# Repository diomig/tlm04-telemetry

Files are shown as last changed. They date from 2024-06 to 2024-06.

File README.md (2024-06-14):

# Telemetry System for TLM03e and TLM04e

In automotive racing, every second counts when it comes to winning a race. If the pilot brakes too early or makes too wide of a turn, they risk being overtaken and loosing the advantage. Thus, it is of major interest to be aware of how the vehicle behaves on track. In professional automotive sports, such as Formula 1 and MotoGP, the teams resort to the use of telemetry to improve machine and rider performance. 
This project refers to the telemetry system developed for an electric racing motorcycle prototype, built by Portuguese students at Instituto Superior Técnico (IST). 
[TLMoto](https://tlmoto.tecnico.ulisboa.pt/) is a team made of students, mainly from IST, which is dedicated to projecting, building and racing electric motorcycles for international competitions around the world, like the one shown in the figure bellow.

This telemetry system is equipped with various sensors and communicates with the other sub-systems within the motorcycle, in order to collect and log as much information as possible. This piece of equipment has allowed the team at TLMoto to better understand the behavior of the prototype, advise the rider and also to troubleshoot other parts of the vehicle.

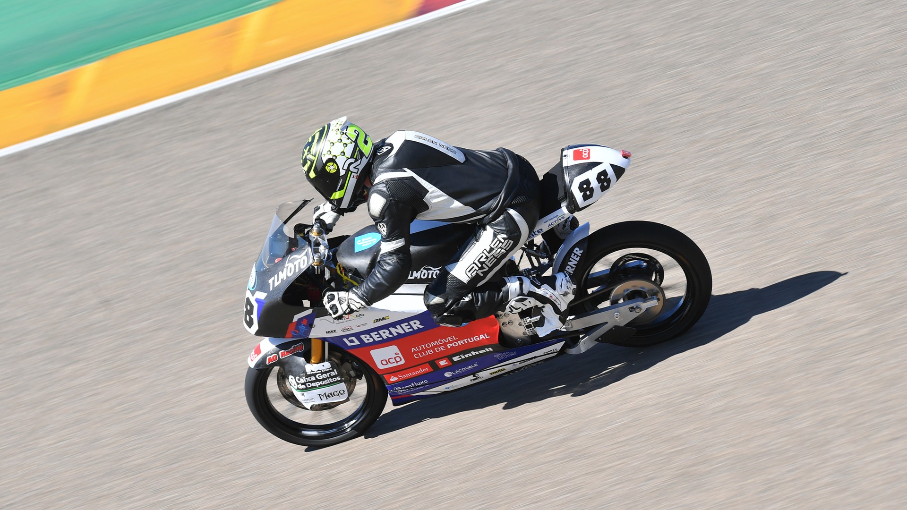
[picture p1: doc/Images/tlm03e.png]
TLM03e prototype TLM03e


## What is telemetry?
Telemetry is the measurement of data from a distant object or vehicle, and, in many cases, the transmission of those measurements to a ground-station or database. However, all the competitions (like MotoStudent:tm:, Moto Engineering Italy:tm:, etc.) prohibit the use of live telemetry data transmission, as is the case of the professional MotoGP. As stated on the official regulation documents of those competitions, the telemetry data obtained from the prototype must only be acquired during pit-stops. 

The telemetry acquisition is a very important sub-system of the prototype, as it allows the team to have an accurate description of its behaviour in tests and races, as well as to provide feedback and suggestions to the pilot. It also plays a big roll in understanding what could be altered on the current prototype or what could be improved on the next one.

## Project Description and Requirements
This system is intended to measure, manage, store and finally transmit all the acquired data, which is then sent to an external computer to be properly processed and displayed to the pit crew. The objective is to extract the maximum of useful data to accurately characterize the prototype, while avoiding to overload the system. For this reason, not only the physical quantities to obtain must be chosen wisely, but also the system must be fast and robust so the loss of information is minimal. It should collect information about the dynamic, mechanical, electrical and thermal aspects of the motorcycle, as well as the control inputs given by the pilot, in order to observe how the prototype actually responds to commands and compare it with the expected response.

The most important items to quantify are: velocity, accelerations, RPM, suspension travel, temperatures of the motor and controller, temperatures of the battery packs, voltages of the battery packs, current from the battery, accelerator and brakes inputs and position over time so the parameters can be analysed along the track. Some other values that are obtained are, for example: phasor components of the motor current ($I_d$, $I_q$), torque, handlebar steering angle, roll and pitch angles, among others. 

As per the data logging and retrieving, all the acquired values are stored during the laps in an SD card, that can be conveniently removed and plugged in to a computer. Alternatively to the removal of the SD card, the content of the telemetry may be transmitted to the computer via Bluetooth, using the Bluetooth 5.0 module included in the system's last iteration. This is done as such because, as mentioned earlier, distant communication is not allowed by the regulation and the retrieving of the data must be done only within the premises of the box.

## Sensors and other components
Before specifying what sensors to get, it is best to figure what is already available in the prototype that can provide information about the parameters mentioned in the previous section.

### Controller
One very important component for our motorcycle and any other electric vehicle is the controller, which is used as an interface between the accumulator and the motor. The TLM03e uses a \emph{Sevcon Gen4 Size 6} controller to turn the 126V of direct current from the battery into three-phase AC voltage for the motor. This device is able to control and measure the motor's rotations per minute (RPM), torque and currents, as well as to keep track of the temperatures of the motor and the controller itself. All those parameters are sent to the CAN bus (Controller Area Network) that connects all the sub-systems of the Low Voltage System and then received by the telemetry module. 

### Battery Management System (BMS)
The accumulator is a set of many battery cells in series and parallel configurations. The one in TLM03e is divided in five battery packs, each made of six sets of cells, and they must be constantly monitored and balanced between each other. This task is accomplished by yet another sub-system called BMS (Battery Management System). The BMS measures the voltage of every individual set of cells and the temperature in three points of every pack. The voltage and temperature values obtained by the BMS are sent to the CAN bus.

### Sensors On-board
The position coordinates of the motorcycle along the track are collected by a GPS module. The chosen module was a GPS 4 Click from MikroE, which has a reasonably good accuracy and can provide an update rate of up to 10 Hz. It outputs messages in the NMEA format with information about the coordinates, UTC time and estimated velocity. We use a "mouse" antenna outside the carbon fiber fairing to avoid RF shielding.

The accelerations and rotation angles -- mainly from pitch and roll -- acting on the motorcycle are measured by an Inertial Measurement Unit, or  IMU, based on the ICM-20948 microchip. It includes a three axis accelerometer, a three axis gyroscope and a three axis magnetometer, thus providing nine degrees of freedom.

The suspension travel is obtained with the use of two linear potentiometers, one for the front suspension and one for rear one. A linear potentiometer translates a variable resistance into a linear displacement. This solution requires constant contact between the wiper and the resistive path, which may reduce durability due to friction. An alternative would be a LVDT, however this uses AC signals, requiring more complex implementation on the circuit.

The accelerator handle includes a rotary potentiometer in order to measure the acceleration inputs from the pilot. Its terminals are directly connected to the controller as this is what will determine the mechanical power requested to the motor. The value corresponding to the accelerator knob is also sent to the telemetry system via CAN.

It is noteworthy to mention that our prototype does not have a gearbox, much like the vast majority of electric vehicles, meaning that the linear velocity can very easily be calculated from the motor RPM. This is due to the direct link between the motor shaft and the wheel sprocket, as shown in the figure below. In fact, the velocity is directly proportional to the RPM according to the following expression: 

$$ v[km/h] = \frac{rpm\times2\pi\times r_{wheel}}{60}\times R_G\times \frac{3600}{1000}     $$

where $r_{wheel}$ is the outer radius of the tire and $R_G$ is the gear ratio used for this conversion.

<p align="center">
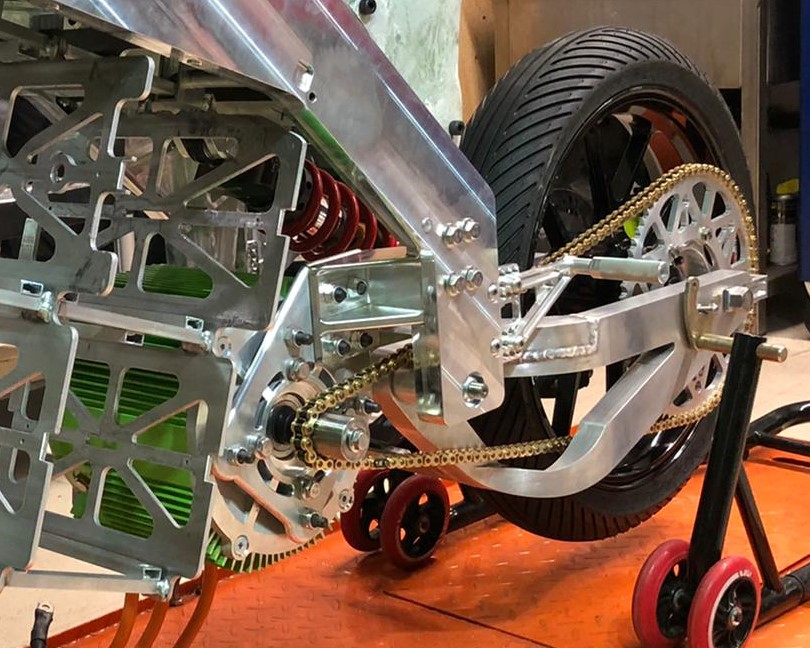
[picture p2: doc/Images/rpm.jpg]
Link between the motor shaft and the wheel sprocket
    
</p>

## PCB
The schematic and layout were made in Altium Designer, the board was manufactured at JLCPCB and it was soldered at TLMoto's workshop in IST. The figure represents only the top layer of the PCB, so some connections are not visible because they are in the bottom layer.

This board includes all sensors and components described above, all commanded by a STM32 microcontroller at the very center. The microcontroller is responsible for collecting, buffering and periodically loading the data to the SD card. It also includes a CAN transceiver and dual Ethernet port for the CAN bus and also for power.

The board operates at 3.3V and requires 5V for some devices. It may be powered through a mini-USB, while programming and debugging, but during its normal operation, it is supplied by the bus that connects the whole Low Voltage System of the motorcycle.

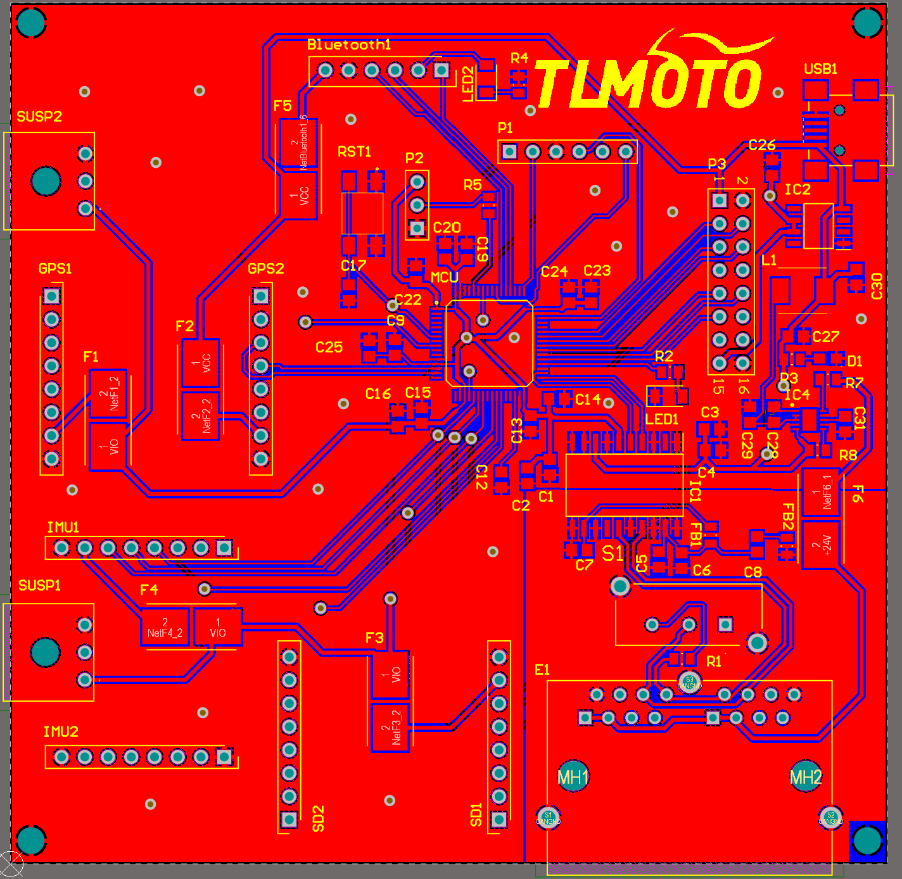
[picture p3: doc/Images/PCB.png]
PCB


## Data Handling and Integration with other subsystems

The GPS module sends the time, coordinates and speed via UART in the format of NMEA strings. 
The CAN messages are arranged according to this table. 

<table>
  <thead>
    <tr>
      <th rowspan="2">CAN ID</th>
      <th colspan="8">Bytes</th>
    </tr>
    <tr>
      <th>B1</th>
      <th>B2</th>
      <th>B3</th>
      <th>B4</th>
      <th>B5</th>
      <th>B6</th>
      <th>B7</th>
      <th>B8</th>
    </tr>
  </thead>
  <tbody>
    <tr>
      <td>11</td>
      <td colspan="2">Target $I_d$</td>
      <td colspan="2">Target $I_q$</td>
      <td colspan="2">$I_f$</td>
      <td colspan="2">$I_q$</td>
    </tr>
    <tr>
      <td>12</td>
      <td colspan="2">$U_d$</td>
      <td colspan="2">$U_q$</td>
      <td colspan="2">Motor PWM</td>
      <td colspan="2">AC Volt.</td>
    </tr>
    <tr>
      <td>13</td>
      <td colspan="2">AC Curr.</td>
      <td colspan="2">Max $I_q$</td>
      <td colspan="2">Motor Temp.</td>
      <td colspan="2">Battery Volt.</td>
    </tr>
    <tr>
      <td>14</td>
      <td colspan="2">Cap. Volt.</td>
      <td colspan="2">Controller Temp.</td>
      <td colspan="2">Battery Curr.</td>
      <td colspan="2">Torque</td>
    </tr>
    <tr>
      <td>15</td>
      <td colspan="4">RPM</td>
      <td colspan="2">Throttle Volt.</td>
      <td colspan="2">Throttle Value</td>
    </tr>
    <tr>
      <td>51</td>
      <td colspan="8">Cell Voltages of Pack 1</td>
    </tr>
    <tr>
      <td>52</td>
      <td colspan="8">Cell Voltages of Pack 2</td>
    </tr>
    <tr>
      <td>53</td>
      <td colspan="8">Cell Voltages of Pack 3</td>
    </tr>
    <tr>
      <td>54</td>
      <td colspan="8">Cell Voltages of Pack 4</td>
    </tr>
    <tr>
      <td>55</td>
      <td colspan="8">Cell Voltages of Pack 5</td>
    </tr>
    <tr>
      <td>121</td>
      <td colspan="8">Temperatures in Packs 1 and 2</td>
    </tr>
    <tr>
      <td>122</td>
      <td colspan="8">Temperatures in Packs 3 and 4</td>
    </tr>
    <tr>
      <td>123</td>
      <td colspan="8">Temperatures in Pack 5</td>
    </tr>
  </tbody>
</table>

All the collected parameters are organized and logged into the SD card, in a CSV file (comma-separated values). This file is then loaded to a computer, which will process the data and generate the desired graphs. 

## Test Results

In this section are shown a few of the many graphs generated from the data acquired while testing the TLM03e in the KIRO (Kartódromo Internacional da Região Oeste) track in Bombarral. Although the telemetry system described in this document was made for TLM04e, this motorcycle is still in development. Thus, the tests were performed with the previous prototype, since this is a modular block compatible with the rest of the system. 

Velocity along the track | Throttle position along the track
--- | ---
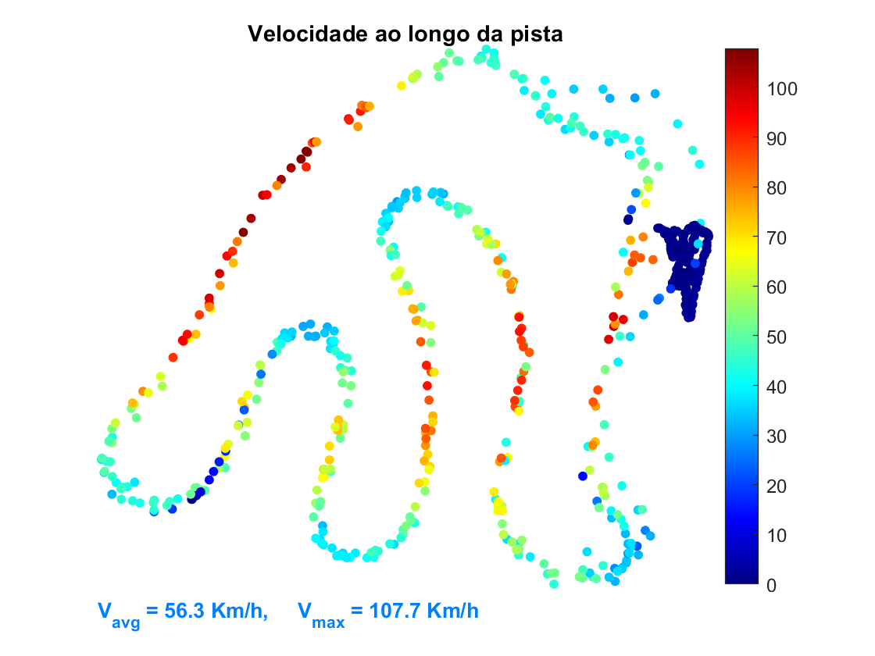
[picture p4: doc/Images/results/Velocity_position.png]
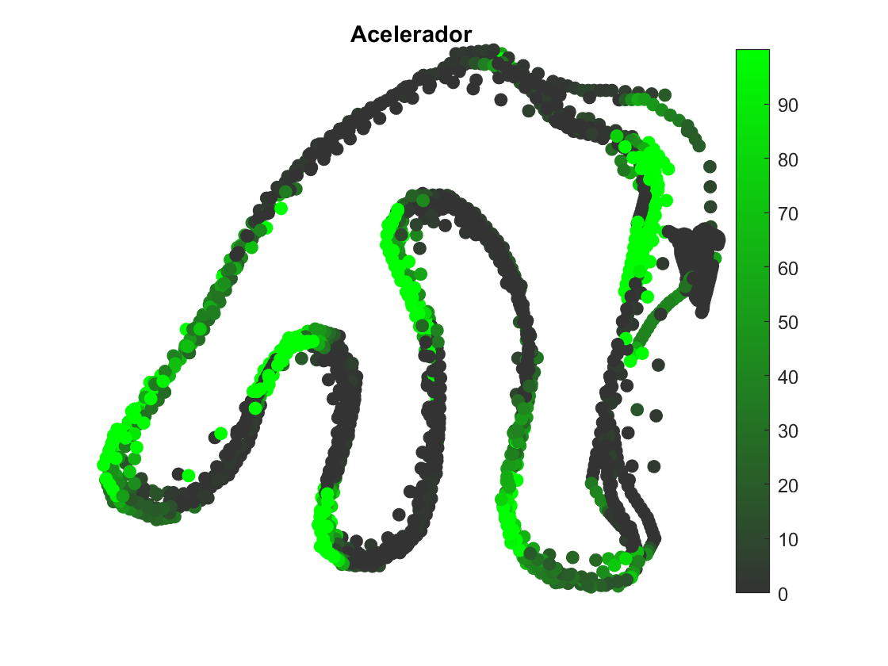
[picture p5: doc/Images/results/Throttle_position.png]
 |  

Speed reaction to the throttle | Motor currents (I_d and I_q)
--- | ---
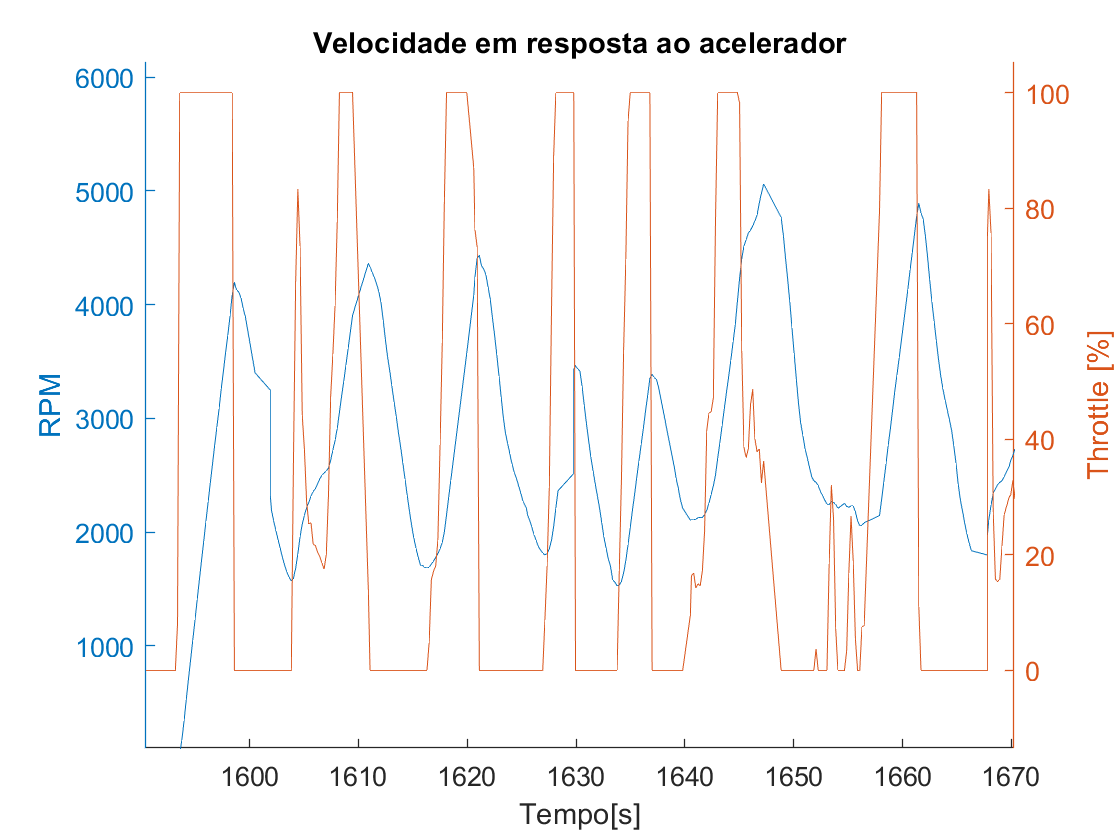
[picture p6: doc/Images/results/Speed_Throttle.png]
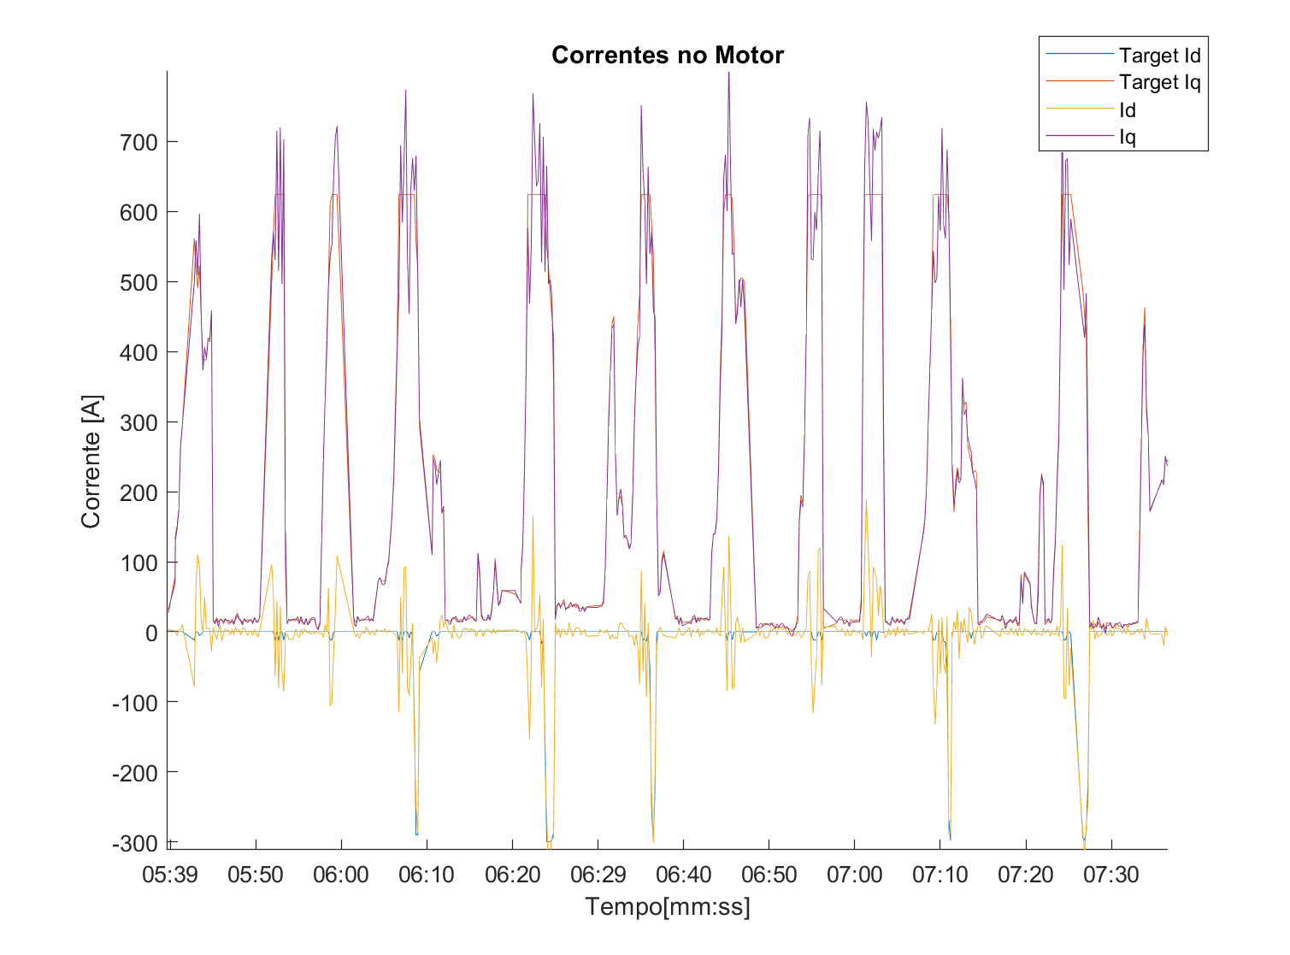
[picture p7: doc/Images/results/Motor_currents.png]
 | 

Battery Voltage | Temperatures of the Motor and Controller
--- | ---
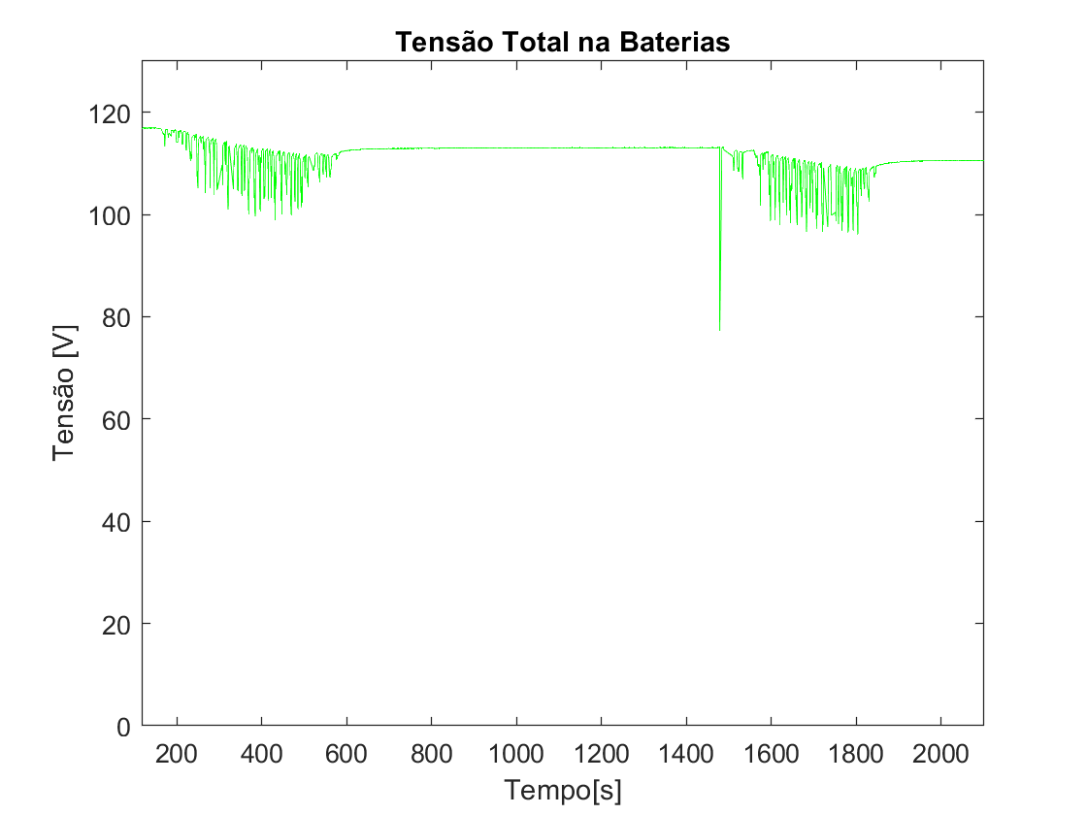
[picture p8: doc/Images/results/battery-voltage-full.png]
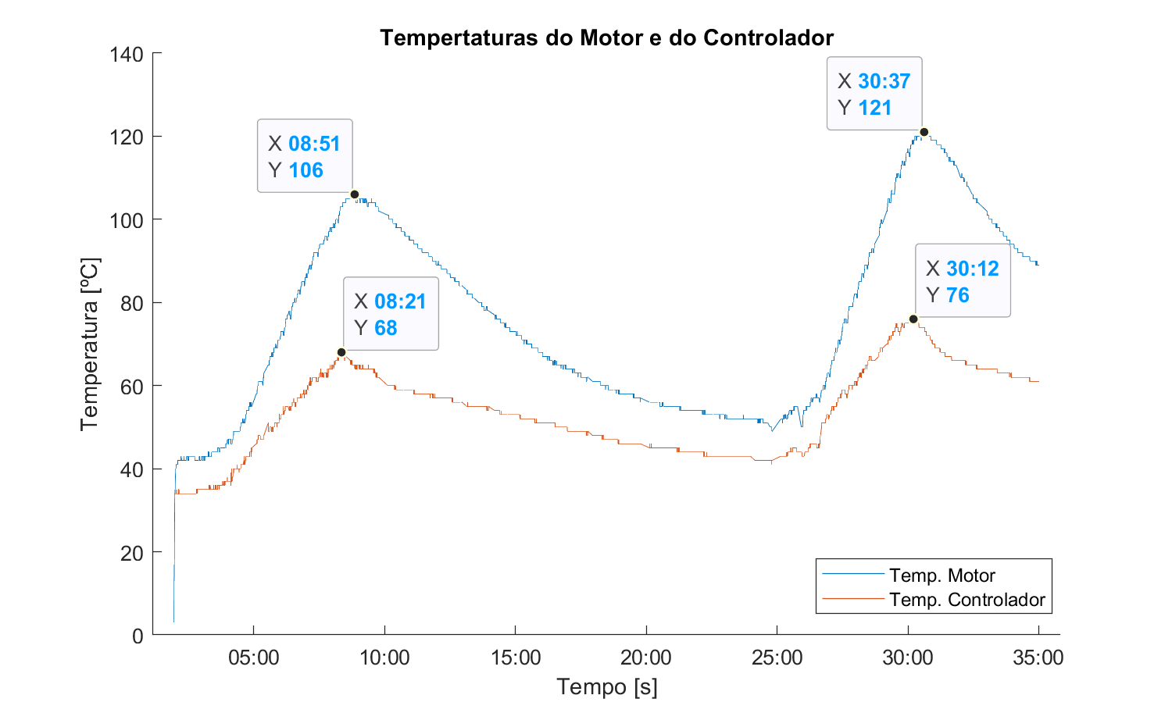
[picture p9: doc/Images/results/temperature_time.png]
 |  

### Motor temperature along the track
<p float="left">
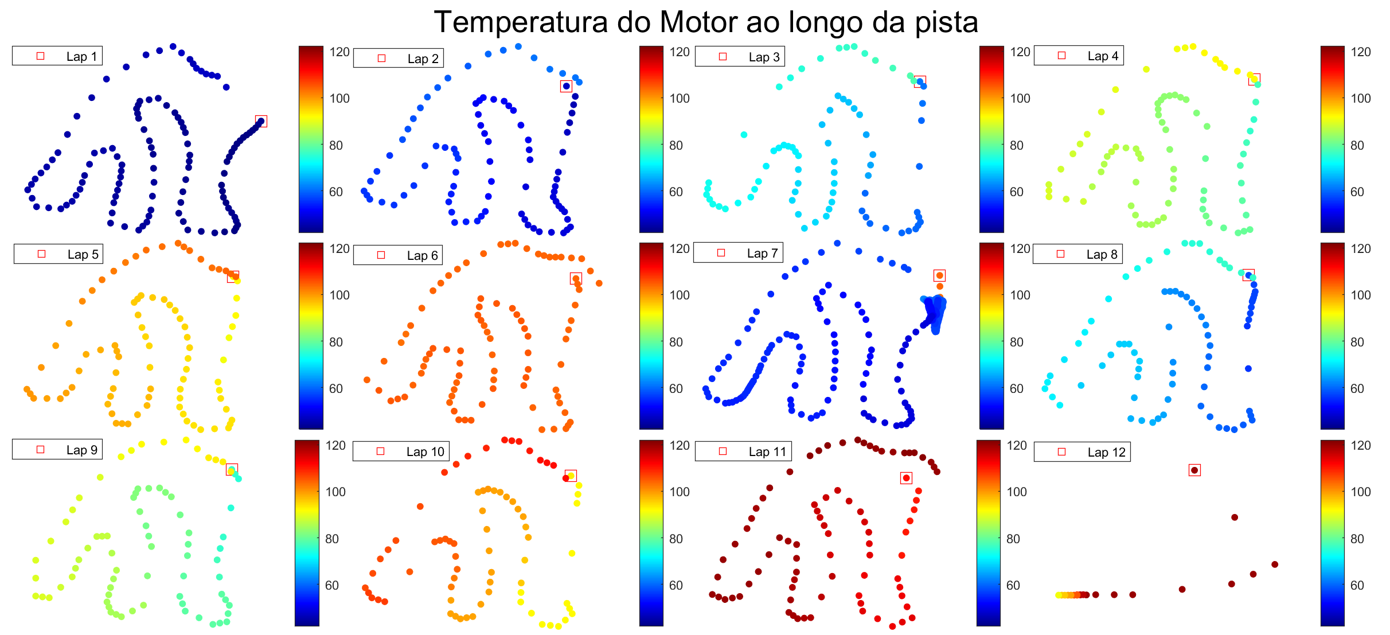
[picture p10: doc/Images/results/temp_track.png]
  
</p>

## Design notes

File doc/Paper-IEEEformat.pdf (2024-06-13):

MEE SOFTSKILLS II, 2022-2023 | 1

# Data Acquisition and Logging System for Electric Motorcycle Prototype

Diogo Lu´ıs
Dept. of Electrical and Computers Engineering IST, University of Lisbon
Lisbon, Portugal
diogo.m.luis@tecnico.ulisboa.pt

Abstract—In automotive racing, every second counts when it comes to winning a race. If the pilot brakes too early or makes too wide of a turn, they risk being overtaken and loosing the advantage. Thus, it is of major interest to be aware of how the vehicle behaves on track. In professional automotive sports, such as Formula 1 and MotoGP, the teams resort to the use of telemetry to improve machine and rider performance. This article refers to the telemetry system developed for an electric racing motorcycle prototype, built by Portuguese students at Instituto Superior Tecnico. This telemetry system is equipped with various ´ sensors and communicates with the other sub-systems within the motorcycle, in order to collect and log as much information as possible. This piece of equipment has allowed the team at TLMoto to better understand the behavior of the prototype, advise the rider and also to troubleshoot other parts of the vehicle.

Index Terms—telemetry, data acquisition, data logging, sensors, racing motorcycle

I. INTRODUCTION
T
LMOTO is a team made of students, mainly from IST, which is dedicated to projecting, building and racing electric motorcycles for international competitions around the world, like the one shown in figure 1. This team is made up of various technical and non-technical departments such as: aerodynamics and cooling, dynamics, electronics, powertrain, structures, marketing, management and sponsors. This project is developed within the scope of the electronics department, more specifically, the telemetry sub-department. Telemetry is the measurement of data from a distant object or vehicle, and, in many cases, the transmission of those measurements to a ground-station or database [1]. However, all the competitions (like MotoStudent™, Moto Engineering Italy™, etc.) prohibit the use of live telemetry data transmission, as is the case of the professional MotoGP. As stated on the official regulation documents of those competitions, the telemetry data obtained from the prototype must only be acquired during pit-stops. This paper describes the development and functioning of the telemetry system built for the next TLMoto prototype, TLM04e. The telemetry acquisition is a very important sub-system of the prototype, as it allows the team to have an accurate description of its behaviour in tests and races, as well as to provide feedback and suggestions to the pilot. It also plays a big roll in understanding what could be altered on the current prototype or what could be improved on the next one [2].


Fig. 1. TLM03e

II. DESIRED FUNCTIONS

This system is intended to measure, manage, store and finally transmit all the acquired data, which is then sent to an external computer to be properly processed and displayed to the pit crew. The objective is to extract the maximum of useful data to accurately characterize the prototype, while avoiding to overload the system. For this reason, not only the physical quantities to obtain must be chosen wisely, but also the system must be fast and robust so the loss of information is minimal. It should collect information about the dynamic, mechanical, electrical and thermal aspects of the motorcycle, as well as the control inputs given by the pilot, in order to observe how the prototype actually responds to commands and compare it with the expected response.
The most important items to quantify are: velocity, accelerations, RPM, suspension travel, temperatures of the motor and controller, temperatures of the battery packs, voltages of the battery packs, current from the battery, accelerator and brakes inputs and position over time so the parameters can be analysed along the track. Some other values that are obtained are, for example: phasor components of the motor current (Id, Iq), torque, handlebar steering angle, roll and pitch angles, among others.
As per the data logging and retrieving, all the acquired values are stored during the laps in an SD card, that can be conveniently removed and plugged in to a computer. Alternatively to the removal of the SD card, the content of the telemetry may be transmitted to the computer via Bluetooth, using the Bluetooth 5.0 module included in the system’s last iteration. This is done as such because, as mentioned earlier, distant communication is not allowed by the regulation and the retrieving of the data must be done only within the premises of the box.

III. SENSORS AND OTHER COMPONENTS
Before specifying what sensors to get, it is best to figure what is already available in the prototype that can provide information about the parameters mentioned in section II.
A. Controller
One very important component for our motorcycle and any other electric vehicle is the controller [3], which is used as an interface between the accumulator and the motor. The TLM03e uses a Sevcon Gen4 Size 6 controller to turn the 126V of direct current from the battery into three-phase AC voltage for the motor. This device is able to control and measure the motor’s rotations per minute (RPM), torque and currents, as well as to keep track of the temperatures of the motor and the controller itself. All those parameters are sent to the CAN bus (Controller Area Network) that connects all the sub-systems of the Low Voltage System and then received by the telemetry module.
B. Battery Management System
The accumulator is a set of many battery cells in series and parallel configurations. The one in TLM03e is divided in five battery packs, each made of six sets of cells, and they must be constantly monitored and balanced between each other. This task is accomplished by yet another sub-system called BMS (Battery Management System)[4]. The BMS measures the voltage of every individual set of cells and the temperature in three points of every pack. The voltage and temperature values obtained by the BMS are sent to the CAN bus.
C. On-board Sensors
The position coordinates of the motorcycle along the track are collected by a GPS module. The chosen module was a GPS 4 Click from MikroE, which has a reasonably good accuracy and can provide an update rate of up to 10 Hz. It outputs messages in the NMEA format with information about the coordinates, UTC time and estimated velocity. We use a ”mouse” antenna outside the carbon fiber fairing to avoid RF shielding.
The accelerations and rotation angles – mainly from pitch and roll – acting on the motorcycle are measured by an Inertial Measurement Unit, or IMU, based on the ICM-20948 microchip. It includes a three axis accelerometer, a three axis gyroscope and a three axis magnetometer, thus providing nine degrees of freedom.
The suspension travel is obtained with the use of two linear potentiometers, one for the front suspension and one for rear one. A linear potentiometer translates a variable resistance into a linear displacement. This solution requires constant contact between the wiper and the resistive path, which may reduce durability due to friction. An alternative would be a

LVDT, however this uses AC signals, requiring more complex implementation on the circuit.
The accelerator handle includes a rotary potentiometer in order to measure the acceleration inputs from the pilot. Its terminals are directly connected to the controller as this is what will determine the mechanical power requested to the motor. The value corresponding to the accelerator knob is also sent to the telemetry system via CAN.

It is noteworthy to mention that our prototype does not have a gearbox, much like the vast majority of electric vehicles, meaning that the linear velocity can very easily be calculated from the motor RPM. This is due to the direct link between the motor shaft and the wheel sprocket, as shown in figure
2. In fact, the velocity is directly proportional to the RPM according to equation 1:

v[km/h] = rpm × 2π × rwheel
60

× RG ×

3600
1000

(1)

where rwheel is the outer radius of the tire and RG is the gear ratio used for this conversion.


Fig. 2. Link between the motor shaft and the wheel sprocket

This method is fairly reliable and allows to get a complementary value of velocity to the GPS with no additional sensors. There is, however, some error associated with the rear wheel drifting on the track, but this appears to be residual as the prototype has considerable downforce [5], specially at high speeds.

IV. HARDWARE AND PCB DESIGN
Figure 3 illustrates the PCB layout from the latest design of the telemetry system. The schematic and layout were made in Altium Designer, the board was manufactured at JLCPCB and it was soldered at TLMoto’s workshop in IST. The figure represents only the top layer of the PCB, so some connections are not visible because they are in the bottom layer.
This board includes all sensors and components described above, all commanded by a STM32 microcontroller at the very center. The microcontroller is responsible for collecting, buffering and periodically loading the data to the SD card. It also includes a CAN transceiver and dual Ethernet port for the CAN bus and also for power.
The board operates at 3.3V and requires 5V for some devices. It may be powered through a mini-USB, while programming and debugging, but during its normal operation, it is supplied by the bus that connects the whole Low Voltage System of the motorcycle.

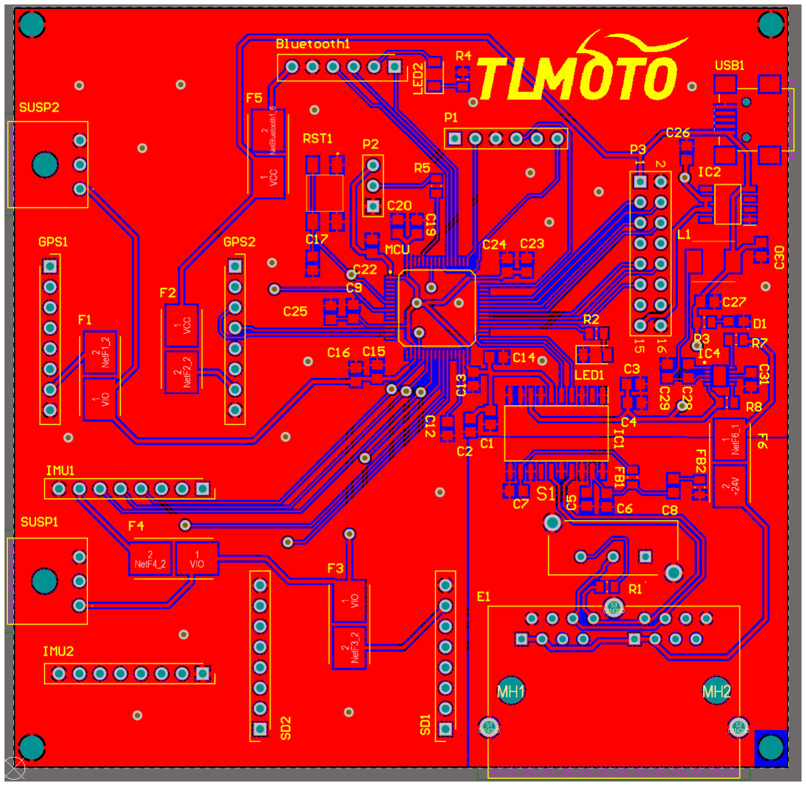
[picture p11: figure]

Fig. 3. Printed Circuit Board of the telemetry system

V. HANDLING THE DATA
The GPS module sends the time, coordinates and speed via UART in the format of NMEA strings. The CAN messages are arranged according to table I.

TABLE I
CAN MESSAGES SENT FROM THE CONTROLLER AND FROM THE BMS
CAN ID | Bytes
B1 | B2 | B3 | B4 | B5 | B6 | B7 | B8
11 | Target Id | Target Iq | If | Iq
12 | Ud | Uq | Motor PWM | AC Volt.
13 | AC Curr. | Max Iq | Motor Temp. | Battery Volt.
14 | Cap. Volt. | Controller Temp. | Battery Curr. | Torque
15 | RPM | | Throttle Volt. | Throttle Value
51 | Cell Voltages of Pack 1
52 | Cell Voltages of Pack 2
53 | Cell Voltages of Pack 3
54 | Cell Voltages of Pack 4
55 | Cell Voltages of Pack 5
121 | Temperatures in Packs 1 and 2
122 | Temperatures in Packs 3 and 4
123 | Temperatures in Pack 5

Controller

BMS

All the collected parameters are organized and logged into the SD card, in a CSV file (comma-separated values). This file is then loaded to a computer, which will process the data and generate the desired graphs.

VI. RESULTS
In this section are shown a few of the many graphs generated from the data acquired while testing the TLM03e in the
KIRO (Kartodromo Internacional da Regi ´ | ao Oeste) track in ˜
Bombarral. Although the telemetry system described in this document was made for TLM04e, this motorcycle is still in development. Thus, the tests were performed with the previous prototype, since this is a modular block compatible with the rest of the system.
In figure 4, it is shown the route of the motorcycle, in the shape of the KIRO track. The color of each point represents its instantaneous velocity according to the color bar to the right. From the image it is clear that, predictably, the speed is lower on the turns and substantially increases in straight lines.

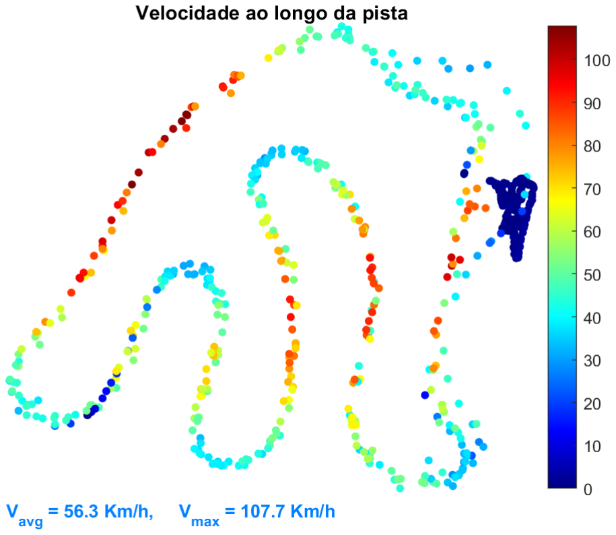
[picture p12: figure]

Fig. 4. Velocity along the track

Figure 5 shows the value of the throttle handle potentiometer along the track. The brightest shade of green means the throttle value is 100% and the darkest shade means that the handle is released. As can be observed, the rider accelerates more at the end of every turn. This information can be interpreted by the pit crew in order to advise the rider.

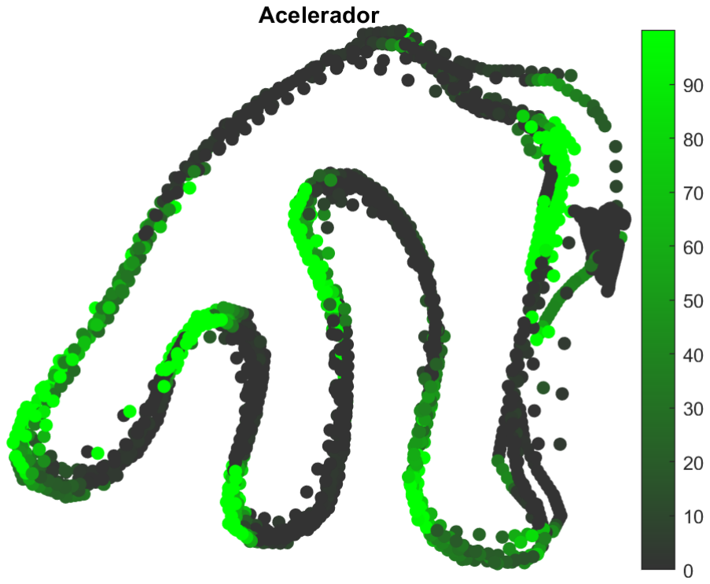
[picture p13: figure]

Fig. 5. Throttle along the track

Figure 6 illustrates how the motor RPM correlates with throttle percentage. When the throttle is set to a constant value, the speed rises at constant rate, when it is released the motorcycle decelerates.


Fig. 6. Relationship between speed and throttle value

Fig. 7 describes the temperature of the motor during a two stage test, where the motorcycle runs for six laps, then stops for about 15 minutes for feedback with the pilot and then goes on for another five laps.

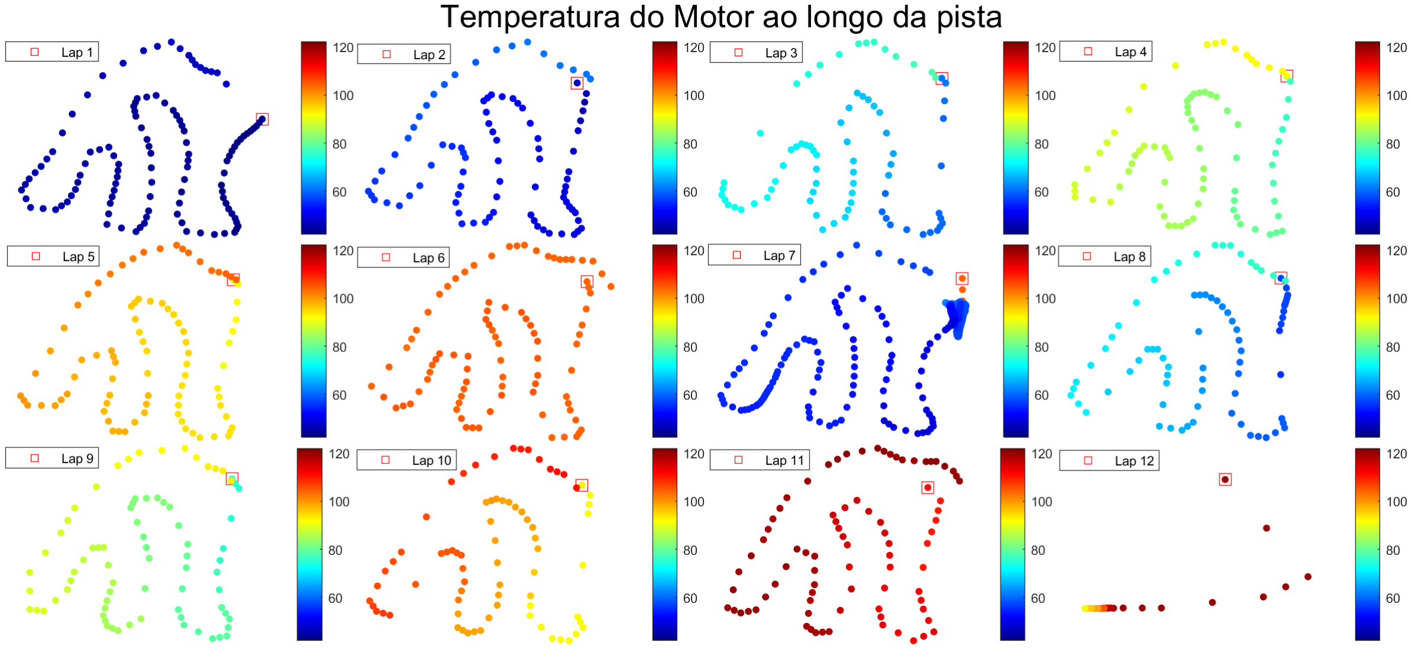
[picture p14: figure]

Fig. 7. Motor temperature along the track

On the first part of the test, the temperature rises gradually, eventually reaching 106◦C. Afterwards, the vehicle returns to the pit (located on the high density area on the right on the ”lap 7” window), where it cools off to below 60◦C. Finally, on the second run the temperature goes up to 121◦C. Figure 8 describes the same test, plotting the temperatures of the motor and the controller over time.

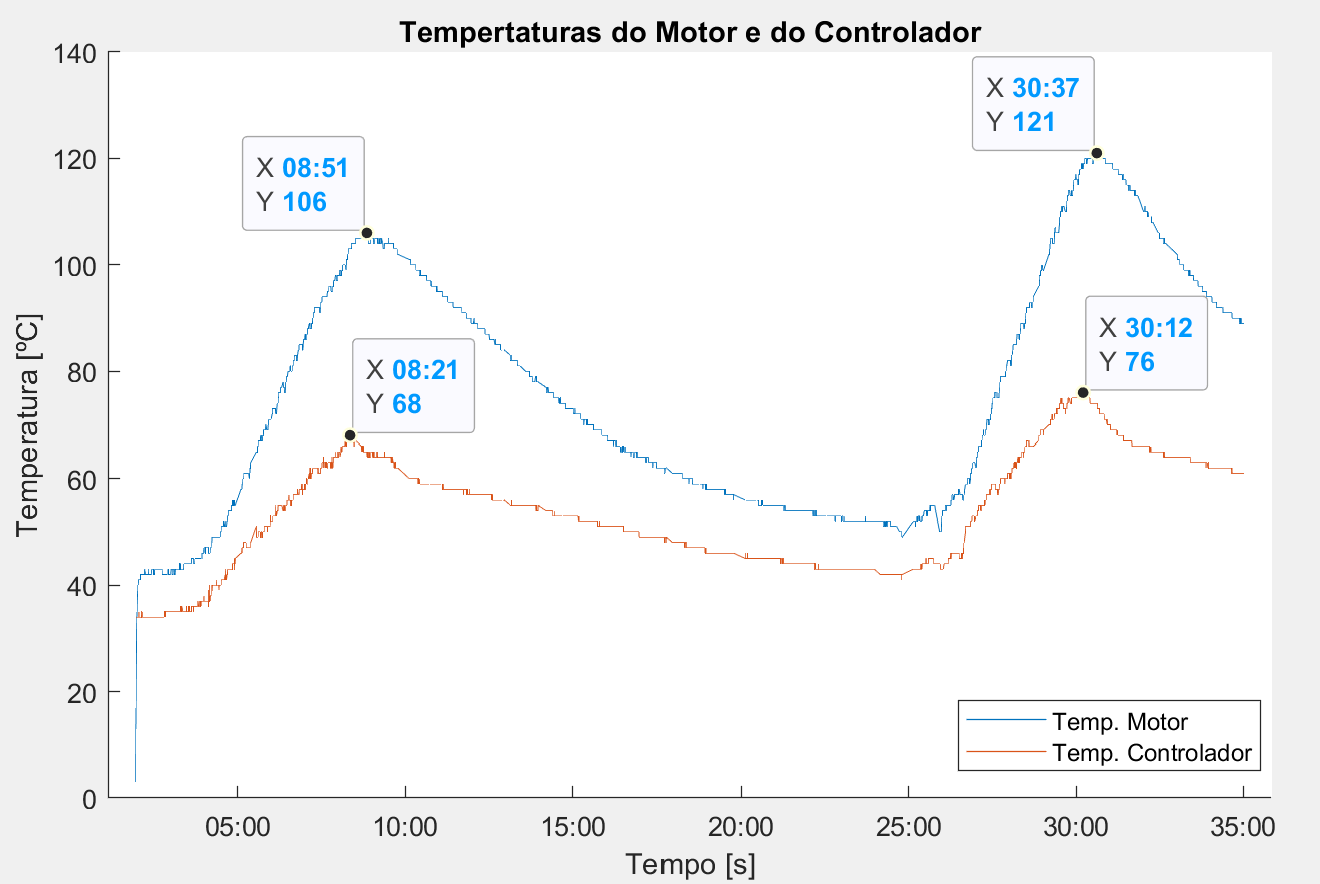
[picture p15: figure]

Fig. 8. Motor and controller temperatures over time

Still from the same set of data, figure 9 demonstrates how the voltage on the battery varies during the test run. The voltage starts off just below 117 V and finishes the test with 110 V. The spiky areas occur when the motorcycle is running and are caused by the current peaks on the High Voltage System.

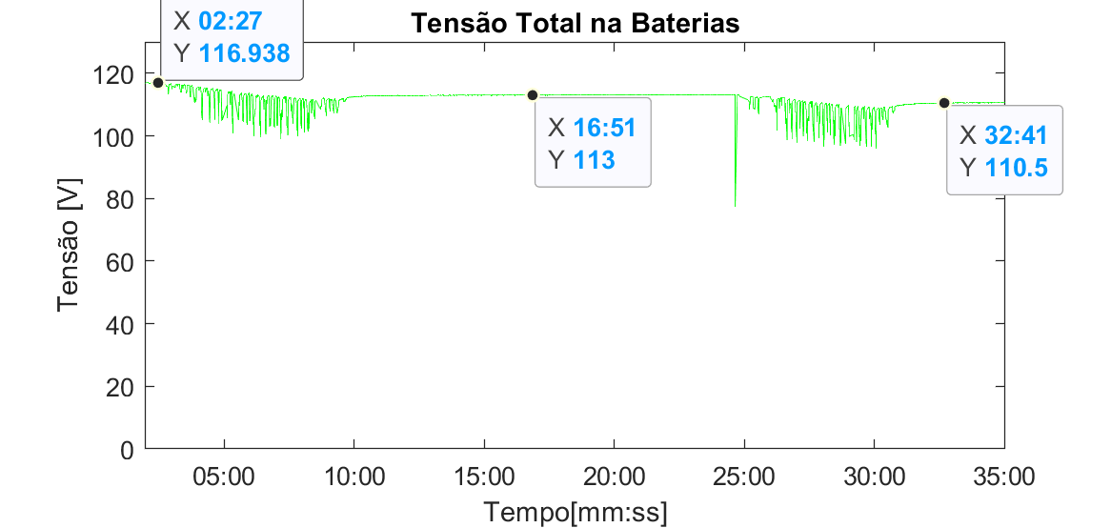
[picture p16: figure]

Fig. 9. Battery Voltage over time

The team was able to generate plenty of graphs just like the ones in this section, allowing to describe these and many other parameters of interest.

VII. CONCLUSION
The telemetry system described in this document serves its purpose of better understanding how the prototype behaves in track and how the rider handles it. It has allowed the team to improve performance, to keep track of important parameters and to display them in a visual and organized disposition. Although this equipment is still in development, it is already being implemented as a sub-system on the current and upcoming prototypes.
However, as can be observed in the results from section VI, there is some occasional data loss, especially on the GPS. We also noticed a few glitches in the values of some acquisitions due to errors in communication. These and other problems will soon be fixed. The telemetry sub-department is also working on a graphical user interface, in order to provide an convenient and intuitive manner of navigating through the desired graphs. It is also relevant to mention the didactic value of this project. The development of this system gathers important aspects of embedded systems, both in the hardware and software components.

REFERENCES

[1] Mitronikas, Epaminondas & Safacas, A. & Tsoumas, Ioannis. (2007). Development of a telemetry system for electric vehicles.
[2] Chandiramani, J. R., Bhandari, S., &amp; Hariprasad, S. A. (2014). Vehicle data acquisition and Telemetry. 2014 Fifth International Conference on Signal and Image Processing. https://doi.org/10.1109/icsip.2014.35
[3] Wang, Haiying & Sun, Tianjun & Zhou, Xingbo & Fan, Qi. (2015). Research on the Electric Vehicle Control System. International Journal of u- and e-Service, Science and Technology. 8. 103-110. 10.14257/ijunesst.2015.8.8.11.
[4] Wei Liu, Tobias Placke, K.T. Chau, Overview of batteries and battery management for electric vehicles, Energy Reports, Volume 8, 2022, Pages 4058-4084, ISSN 2352-4847, https://doi.org/10.1016/j.egyr.2022.03.016
[5] Katz, J., ”Aerodynamic Drag and Downforce of a Competition
Motorcycle,” | SAE | Technical | Paper | 2022-01-0892, | 2022,
https://doi.org/10.4271/2022-01-0892.

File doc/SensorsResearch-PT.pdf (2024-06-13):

Instituto Superior Tecnico ´

TLM04e

# Telemetria

MotoStudent 2023

Escrito por:
Diogo Luís

4 de setembro de 2021

## Índice

1 Velocidade da mota | 2
2 Aceleração | 10
3 GPS | 13
4 Direção | 15
5 Travel das Suspensões | 17
6 Temperatura do Controlador e do Motor | 19
7 Inclinação da Mota | 20
8 Pitch | 21
9 Rotação do Motor | 22
10 Correntes de Alimentação do Motor | 23
11 Percentagem de Acelerador e Travão | 24
12 Extensómetros | 26
13 Tubo de Pitot | 29

1

## 1 Velocidade da mota

Existem diversos métodos que permitem determinar da velocidade linear da mota de forma relativamente precisa, com diferentes graus de complexidade e exatidão. E embora consigamos apenas guardar dados no tempo discreto (o que impossibilita um cálculo de velocidade instantânea 100% fiável) podemos obter boas aproximações.

Encoder

Um Encoder Rotativo é um dispositivo eletromecânico capaz de converter movimentos rotativos em impulsos elétricos de onda quadrada. Este dispositivo gera uma quantidade exata de impulsos por revolução com uma distribuição uniforme dos pulsos ao longo dos 360 graus em torno do eixo. O seu funcionamento consiste na incidência de um feixe de luz sobre um sensor fotossensível (ambos com posições fixas) e um disco rotativo entre eles (Figura 1). Esse disco,

apresenta barras transparentes e barras opacas nas extremidades para permitir a passagem e o bloqueio do feixe de luz, respetivamente.

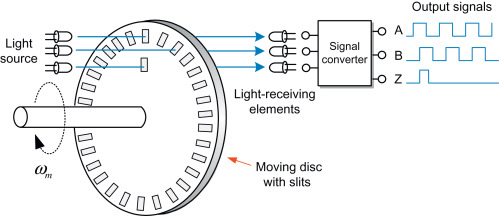
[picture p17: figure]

Figura 1: Esquema de funcionamento

Existem também encoders com mais que uma faixa de barras cujo padrão segue a codificação binária de Gray, pelo que cada uma dessas faixas corresponde a um bit cujo estado é definido pela luminosidade incidente no respetivo sensor. Esse tipo de encoder está mais direcionado para seguir a posição mais facilmente, associando um código binário a cada região do disco. No entanto, para a TLM04e, o interesse no encoder restringe-se apenas ao cálculo da velocidade (e possivelmente da aceleração), portanto é preferível o tipo mais simples.

Geralmente, produzem três sinais quadrados na saída, sendo que dois deles têm a mesma frequência mas desfasados de ±90◦
(normalmente denominados pelas letras A e B), e o outro apresenta um impulso por cada rotação(normalmente denominado por Z). Os sinais A e B dizem respeito à passagem/bloqueio dos feixes luminosos e a frequência dos impulsos depende da

velocidade angular do disco. O motivo de se extrair dois sinais desfasados é detetar o sentido da rotação do veio, o que não tem grande interesse para uma mota, tanto que apenas precisaremos

2

de um deles. O sinal Z tem como objetivo registar cada volta que o disco gira sobre o eixo ao longo do tempo.
Ao analisar as mudanças de estado do sinal de pulso A ou B em função do tempo, é possível

estimar a velocidade angular da rotação do disco e, consequentemente, podemos determinar a velocidade linear da mota. Para isto, seria importante ter em conta a forma que o encoder é incorporado no protótipo e calcular a relação de proporcionalidade entre a velocidade de rotação do veio do encoder e a velocidade angular da roda. A precisão desta análise depende da quantidade de fendas no disco, mas está limitada pela frequência da amostragem permitida pelo microcontrolador.

(a)

(b)

Figura 2: Encoder

E essencial que os impulsos sejam detetados assim que ocorre a mudança de estado de LOW ´

para HIGH (rising edge) ou de HIGH para LOW (falling edge). Por essa razão, o sinal A do encoder deve ser definido no software como um sinal de interrupção (interrupt-on-input-change), o que significa que, assim que o impulso ascendente (ou descendente) for detetado, o MCU inter-

rompe o que está a fazer nesse momento e executa a função que está associada a essa interrupção. Caso a deteção dos impulsos fosse feita ciclicamente com o resto do programa, os intervalos entre as medições dependeriam do tempo de execução do algoritmo, que está dependente de vários fatores como o número de acessos de memória, validações, operações aritméticas, alocações e outras instruções básicas feitas pelo processador em cada iteração do programa. Isto tornaria impossível detetar ao certo quando ocorreu o início do impulso e nem nos dá a garantia de que estamos a considerar todos os eventos sem saltar nenhum, o que iria corromper os resultados. Com o STM32, basta ligar o sinal A e, se necessário, o sinal Z aos pins GPIO adequados do microcontrolador. Quanto ao software, penso que dê para utilizar a biblioteca ”PinDetect.h”para lidar com as interrupções, já que é bastante prático para definir se pretendemos detetar o rising edge ou o falling edge e associar uma função callback para executar na ocorrência de cada impulso.
E apenas preciso ter em conta o estado do sinal definindo o pin como ´ | PullDown (default) ou

PullUp dependendo do tipo de encoder, e também definir os intervalos de tempo entre cada

3

amostra (sampling period). O sampling period deve ser um valor baixo, pois a frequência de

amostragem do microcontrolador tem de ser muito superior ao ritmo de eventos do sinal de pulso observado no encoder. Na biblioteca ”PinDetect.h”, o valor default do sampling period é 20ms, mas neste caso tem de ser muito menor.
De modo a visualizar mais facilmente o problema, convém ter uma noção da ordem de grandeza que está associada aos valores com que vamos lidar. Para estabelecer uma margem de segurança, devemos considerar um cenário extremo que nos permita majorar o limite do sampling period. Imaginemos então que a mota viaja a uma velocidade v = 300km/h, que seria uma velocidade bastante elevada para uma mota elétrica (o topspeed nas MotoE é 270). Se o diâmetro exterior do pneu for 17”, a velocidade angular da roda é de aproximadamente ω = 386rad/s, equivalente a 3686 rpm. Podemos calcular o intervalo de tempo entre cada pulso de encoder (te)

através da expressão

te =

2π
ωN

(1)

em que N é o número de pulsos por rotação (ppr) do encoder utilizado (tem a ver com o número de fendas no disco). Se o encoder for de 100 ppr, por exemplo, o te será cerca de 160µs. O microcontrolador que estamos a usar (STM32F446RE) permite-nos atingir frequências de amostragem na ordem dos Megahertz (MHz), o torna possível obter uma boa precisão. Contudo, há que entender que o tempo de amostragem (sampling period, ts) tem de ser muito inferior a te, ou seja, ts << te, portanto, para velocidades elevadas, o número de eventos por revolução (N)

não deve ser muito elevado.

Encoders rotativos permitem-nos fazer uma medição indireta da velocidade linear da mota a partir da variação de um sinal de pulso digital em função do tempo, mas a interpretação dos dados pode ser feita de mais que uma maneira. Destacam-se dois métodos para interpretar a saída do encoder, designados Pulse Timing e Pulse Counting.

Pulse timing

A primeira abordagem consiste em contar o intervalo de tempo entre cada evento do sinal A do encoder. Um sinal de clock de alta frequência é contado durante um período do encoder e a partir daí determina-se o tempo que levou entre dois impulsos do sinal A. Por outras palavras, consiste em fixar uma distância constante, associada ao ângulo do setor circular formado por quaisquer duas fendas consecutivas do disco, e medir o tempo que demora a percorrer essa distância.
O número de ciclos do clock que são contados (c), dividido pela frequência do clock (f), fornece o tempo para o período do encoder (o tempo para girar um passo). Considerando novamente N como o número de pulsos por rotação (ppr) do dispositivo utilizado, a velocidade angular do

4

encoder é dada por

ωe =

2π
N

f
c

(2)

Em seguida, ter-se-ia de obter a velocidade angular da roda da mota e por fim a velocidade linear. Ou melhor, para poupar tempo de execução, encontrar a constante k tal que vmota = k × ωe

Para obter o gráfico da velocidade ao longo do tempo, acho que a melhor opção seria simplesmente guardar no cartão SD a sequência de valores obtidos para as contagens dos ciclos clock
(c) e processá-los posteriormente no MATLAB.

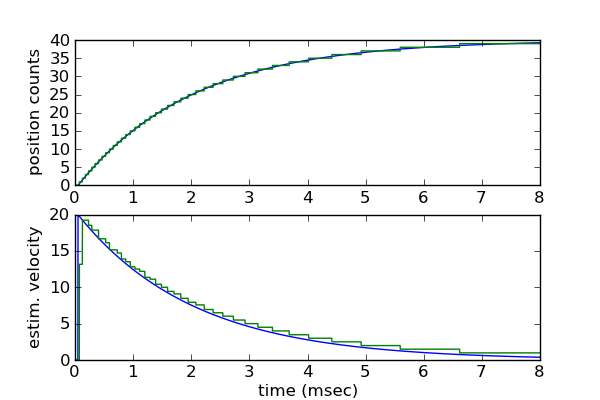
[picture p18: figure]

Figura 3: Obtenção do gráfico da Velocidade

Este método, no entanto, exige que o MCU faça constantemente uma contagem de tempo a alta frequência e guarde valores a cada poucos microsegundos. Isto, para altas velocidades, torna-se quase impossível especialmente tendo em conta que o MCU tem outras tarefas para fazer em simultâneo. Assim sendo, o Pulse Timing apenas oferece boa precisão para velocidades

relativamente baixas.

5

Pulse counting

Uma outra alternativa é contar o número de eventos detetados num dado intervalo de tempo. A técnica do Pulse Counting usa um período de tempo fixo entre medições (∆t) e o número de pulsos (n) que são contados durante esse período para determinar o tempo médio para um pulso. Sabendo o número de pulsos por revolução (N) para o encoder, a sua velocidade angular pode

ser dada por

ωe =

2π
N

n
∆t

(3)

e em seguida consegue-se determinar a velocidade linear da mesma forma anteriormente dita. Assumindo que o intervalo de tempo escolhido é suficientemente pequeno e que a mota não tem alterações de velocidade repentinas devido à inércia, a expressão 3 (e a constante de conversão
k) permite-nos obter uma aproximação bastante boa da velocidade instantânea.

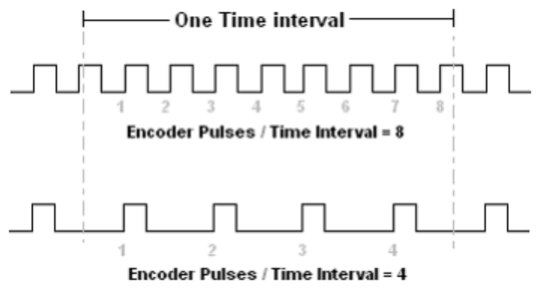
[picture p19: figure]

Figura 4: Pulse Counting

Este método permite-nos escolher o melhor intervalo de medições adequado para o microcontrolador, fornecendo ainda assim resultados fidedignos de velocidade. Concluindo, o Pulse Counting é o método preferencial para grandes velocidades.

Aqui estão algumas das opções mais acessíveis que encontrei:

- SEN0230 - 400ppr, max 5000rpm, ∼ 20€
- CALT ES38 - 100-1000ppr (opção), ∼ 30€
- 62AG-VG - 16ppr, ∼ 15€

6

Wheel Speed Sensor

O wheel speed sensor (WSS) é um dispositivo eletromagnético usado na medição digital da

velocidade na maior parte dos automóveis e motociclos. As grandes vantagens deste sensor são o facto de ser um aparelho muito compacto e a simplicidade de utilização, que é em parte semelhante ao encoder.

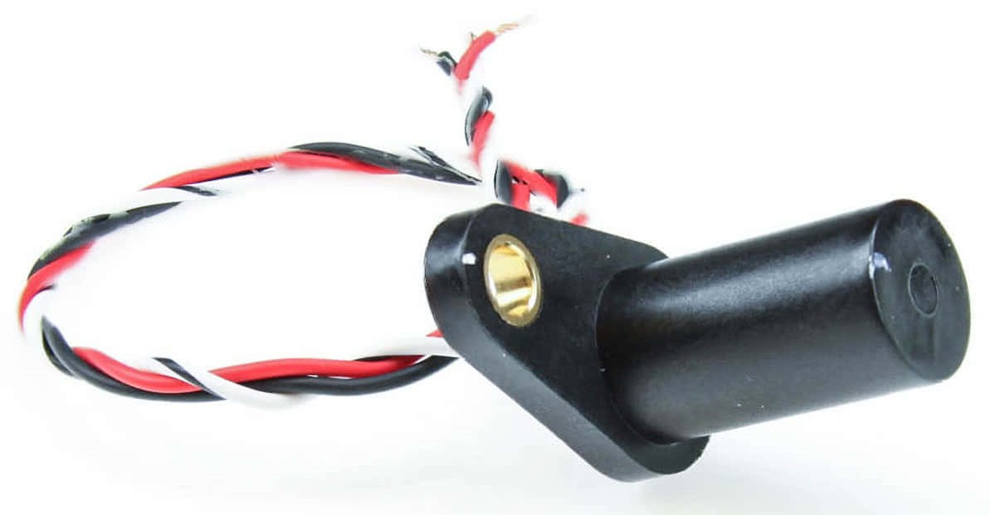
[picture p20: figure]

Figura 5

O WSS consiste numa bobina enrolada em volta de um íman permanente que está apontado para uma roda dentada metálica. Essa roda (ou anel) dentada está ligada ao eixo cuja rotação

se pretende medir, pode ser o próprio eixo de uma roda da mota. O sensor fica numa posição fixa, disposto na forma representada na Figura 6a.

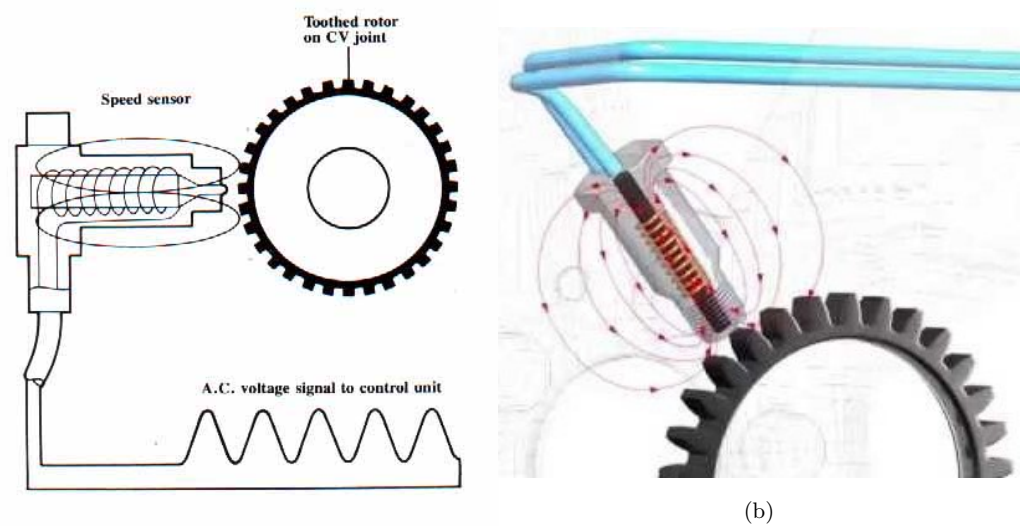
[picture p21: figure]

(a)

Figura 6: Wheel Speed Sensor

7

Este sensor aproveita as propriedades indutivas da bobina para gerar um sinal sinusoidal cuja frequência de oscilação é diretamente proporcional à velocidade de rotação da roda dentada. A corrente gerada no fio da bobina é magneticamente induzido, não havendo nenhum sinal elétrico de entrada. O fenómeno que torna isto possível é princípio físico conhecido como a Lei de Faraday, segundo o qual uma bobina tende a gerar uma força eletrometriz perante variações no fluxo magnético de modo a mantê-lo constante. Por outras palavras, caso haja alguma perturbação no fluxo magnético dentro da bobina, cria-se corrente elétrica.
Como a superfície exterior do anel apresenta vários dentes e buracos alternadamente, a distância mínima entre o sensor e essa superfície altera-se à medida que o anel gira. Essa oscilação causa variações no campo magnético, que por sua vez altera o fluxo magnético e, finalmente, gera um sinal elétrico com a mesma frequência.
Em alternativa à bobina enrolada no íman, alguns WSS usam um sensor de Hall para medir o campo magnético. Para esse tipo de sensor, já é necessário fornecer uma tensão.
Para ambos os tipos de sensor de velocidade, o output é uma onda sinusoidal cuja frequência está diretamente relacionada com a velocidade angular do anel. Depois desse sinal ser processado por um circuito digital, obtém-se uma onda quadrada em que cada impulso corresponde a um dente do anel. A partir daqui, o processo torna-se muito semelhante à análise do sinal do encoder. Usando o método de Pulse Counting, calcula-se a velocidade angular através a expressão 3, sendo que, neste caso, N corresponde ao número de dentes do anel/roda dentada.

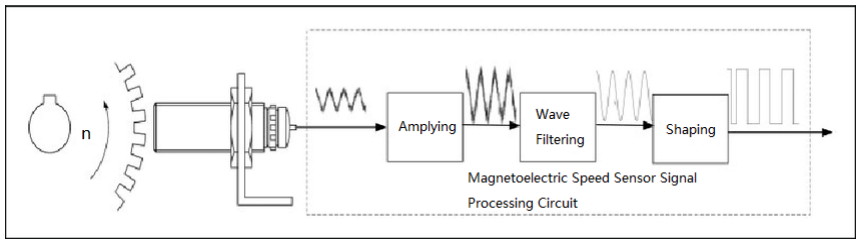
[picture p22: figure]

Figura 7

Alternativas

As próximas soluções estão resumidas na mesma subsecção porque, mais à frente neste documento, falarei sobre elas em diferentes secções. Ambas têm a vantagem comum de os dispositivos necessários já estarem implementados no protótipo, não sendo necessário aparelhos adicionais.

8

GPS - Velocidade

Determinar a velocidade a partir do GPS parece uma solução bastante interessante por várias razões. A primeira é que o GPS sabe a posição exata do veículo num dado instante de tempo, o que torna muito fácil associar a velocidade linear da mota com a localização na pista. Isto pode ser bastante útil na telemetria no sentido em que assim seria possível analisar a velocidade em cada parte da pista.
A segunda vantagem é que esta é a única das soluções aqui apresentadas que não depende da velocidade angular de uma roda para determinar a velocidade linear da mota. Assim evita-se

que pequenos desajustes, como por exemplo o desgaste dos pneus cause algum erro que se vai acumulando por cada revolução da roda.
Outra vantagem é que, como já foi dito, o protótipo vai ter GPS de qualquer das maneiras, ou seja, caso se pretenda ou não usar este método, não implica nenhum aumento na ocupação de espaço.

Controlador

O controlador é o aparelho que regula a alimentação fornecida ao motor, controlando assim a velocidade de rotação do rotor. Como o rotor está ligado a um sistema de engrenagens, que por sua vez está ligado à corrente da mota, conclui-se que a velocidade angular da roda traseira varia linearmente com a velocidade do rotor do motor elétrico. A partir daí, calcula-se facilmente a

velocidade linear da mota.
O número de rotações por minuto que o controlador impõe ao motor pode ser extraído por CAN.

9

## 2 Aceleração

Para além de medir a velocidade a que a mota viaja, também é importante obter os valores de aceleração a que esta está sujeita. A aceleração permite quantificar a variação da velocidade linear, determinar as forças G que atuam sobre o prototipo e, comparando com a aceleração gravítica, o ângulo de inclinação a que este se encontra.

Acelerómetros

O acelerómetro é um sensor bastante comum na tecnologia atual, estando presente em vários dos diversos dispositivos que nos rodeiam, desde drones a telemóveis, e sendo também um aparelho muito útil em desportos motorizados. A razão de este tipo de sensor ser tão utilizado em produtos tão diversos reflete-se nas vantagens que o acelerómetro apresenta sobre todas as outras soluções. Acelerómetros são geralmente muito compactos, acessíveis e podem obter resultados incrivelmente precisos. Normalmente, o acelerómetro anda muito de mãos dadas com o giroscópio, já que ambos têm funcionamentos muito semelhantes. Este facto também se torna bastante vantajoso, pois desta forma, o mesmo sensor permite-nos obter a aceleração linear instantânea associada ao trajeto da mota, bem como a sua inclinação em relação à pista.
Destacam-se dois tipos de acelerómetro com diferentes funcionemntos, os Piezoelétricos e os Sistemas Micro-Eletromecânicos (ou MEMS).

Piezoelétricos

Acelerómetros piezoelétricos usam um cristal com propriedades piezoelétricas, ou seja, quando aplicada uma força sobre esse cristal, o sensor devolve uma tensão elétrica proporcional à força. Este tipo de acelerómetros consiste numa massa (normalmente um disco cerâmico) em cima de

um destes cristais. O peso aparente da massa muda consoante a aceleração a que ela está sujeita, sendo assim possível associar o sinal de saída à aceleração.
No entanto, este sensor não é ideal para a medição da aceleração de um veículo, apresentando grandes desvantagens em relação aos Sistemas Micro-Eletromecânicos. A primeira é o seu tamanho que, mesmo não sendo muito grande, é muito superior aos MEMS. Em segundo lugar, são mais difíceis de utilizar. Em terceiro, esta abordagem envolveria medir tensões, o que envolveria um ADC externo, não podendo ser do MCU porque essas tensões excedem os 5V. E uma das maiores desvantagens é que cada um destes sensores só consegue medir um eixo, significando que seria necessário mais que um acelerómetro, em diferentes configurações, para fazer o mesmo que um acelerómetro micro-eletromecânico. Assim sendo, descartamos esta opção.

10

MEMS

Os acelerómetros mais comuns na maior parte dos dispositivos à nossa volta são do tipo MEMS (Microelectromechanical Systems), e estão contidos num circuito integrado incrivelmente

pequeno.

(a) (b)

Figura 8: Acelerómetro Digital

Um sistema micro-eletromecânico integra elementos mecânicos e eletrónicos localizados num nível de substrato de silício. As dimensões físicas dos dispositivos MEMS podem variar entre a ordem dos micrómetros e dos milímetros, muitas vezes menores que o diâmetro de um fio de cabelo. Da mesma forma, este tipo de tecnologia podem variar em complexidade, desde um estrutura simples sem partes móveis até sistemas extremamente complexos com mecanismos articulados.

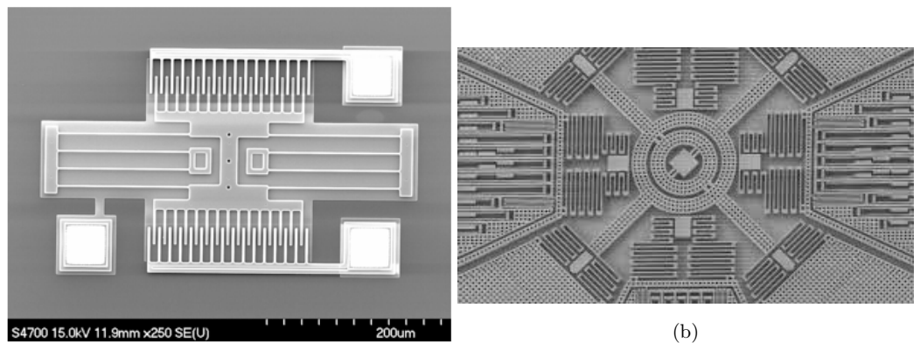
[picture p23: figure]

(a)

Figura 9: Microelectromechanical Systems

11

Os acelerómetros formados por MEMS usam um mecanismo contendo uma placa móvel com uma certa massa, que apresenta barras laterais, como demonstra esquema da figura 10. Para além disso, existem placas fixas entre as barras da placa móvel, que se encontram a um potencial elétrico diferente desta. A figura 9a apresenta uma imagem microscópica do mecanismo descrito. O princípio usado num MEMS para determinar a aceleração é que, aplicada uma aceleração ao objeto, haverá uma força aplicada à placa móvel. No caso de essa aceleração for consequência de um movimento, a placa tenderá a desviar-se para o lado contrário do deslocamento devido à inércia. No caso de o sensor estar sujeito a alguma inclinação, entra em causa a influência da aceleração gravítica. Conforme a aceleração total imposta no sistema, esta placa afasta-se ou aproxima-se mais das barras fixas. O facto de as barras estarem a diferentes potenciais elétricos faz com que se comportem como condensadores e a variação da distância entre elas resulta na variação da capacidade. Medindo estas variações é possível determinar a aceleração que a causou.

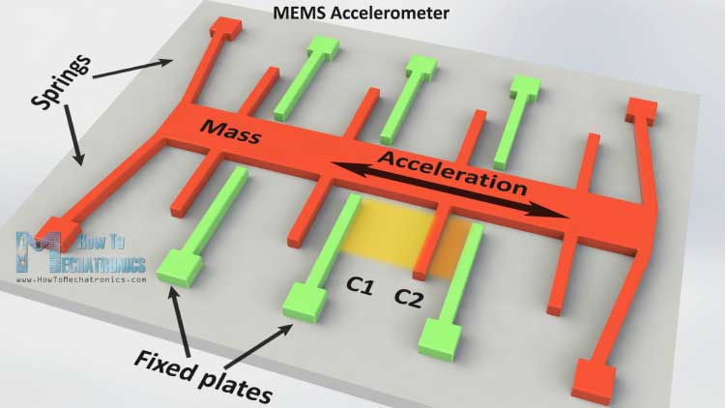
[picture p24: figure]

Figura 10

| ICM-20602 | ADXL335 | ICM-20948
Nº eixos | • 6 | • 3 | • 9
G-rate | • ±2g/ ± 4g/ ± 8g/ ± 16g | • ±3g | • ±2g/ ± 4g/ ± 8g/ ± 16g
ODR¹ | • 3.91-8000Hz | • 0.5-550Hz (eixo z), | • 4.4Hz-1.125kHz
| | 0.5-1600Hz (eixos x e y)
Supply Voltage | • 1.71V-3.45V | • 1.8V-3.6V | • 1.71V-3.6V
Output | • 16 bits | • Sinais Analógicos | • 16 bits
Interfaces | • SPI, I
| 2C | • —————- | • SPI, I 2C

1ODR - Output Data Rate

12

## 3 GPS

Para determinar a posição exata da mota, bem como toda a sua trajetória ao longo da pista, usa-se o sistema GPS. Este sistema consiste numa rede de satélites que enviam continuamente sinais por radiofrequências que podem ser detetadas por recetor GPS. A partir daí, é possível calcular a distância entre o recetor e o satélite. Calculando quatro dessas distâncias, pode-se determinar por triangulação da posição em que o recetor se encontra com um certo grau de precisão.
Com um módulo GPS, obtém-se a cada intervalo de tempo (pode variar de produto para produto) as coordenadas que descrevem a sua localização, sob os valores de longitude, latitude e

altitude, bem como o instante de tempo associado.
Depois de serem calculadas as coordenadas da posição da mota, o módulo GPS deve enviar esses dados para a placa da telemetria. A maior parte dos recetores de GPS devolvem mensagens em série que seguem o formato NMEA, contendo sequências de caracteres de ASCII (no máximo 82 por linha) nas quais se encontram os dados de tempo e coordenadas separados por

vírgulas. Geralmente, a maioria dos recetores tem um update rate 1Hz, significando que recolhe as informações uma vez a cada segundo, e para esse tipo de dispositivo é muito comum a comunicação de dados do pino de transmissão (TX) a uma taxa de 9600 bps ou de 57600 bps.

Outra vantagem do formato NMEA é que este é compatível com vários softwares de mapeamento e navegação, tais como DeLorme Street Atlas, Google Maps, Microsoft MapPoint, entre

outros.
Há também que ter em conta o efeito de blindagem (shielding) de radiação eletromagnética

causados por certos tipos de compósitos, nomeadamente de carbono. Como a TLM04e terá uma carenagem feita de fibra de carbono, ocorre o risco da radiofrequência dos satélites ser bloqueada, pondo em causa os resultados obtidos. Uma solução para este problema seria implementar o recetor por fora da carenagem.
Os módulos do tipo mouse parecem ser os mais apropriados. Estes dispositivos permitem ter o recetor separado do resto dos componentes, não necessitando de estar inserido numa PCB, o que se torna vantajoso pois assim este pode ser colocado algures na mota onde haja melhor sinal. Possivelmente, terá de ser colocado fora do protótipo para evitar o shielding da carenagem. O módulo é ligado por cabos de ligação série sendo capaz de comunicar diretamente com um computador, no caso, com o microcontrolador da placa de telemetria. Os módulos GPS Mouse também têm a vantagem de ser bastante compactos e, como são ligados à PBC por conectores, é bastante fácil inserir/remover, ao contrário dos módulos que são soldados à placa.

13

(a)

(b)

Figura 11: GPS Mouse

Aqui são apresentados alguns exemplos de recetores que oferecem uma boa solução para a implementação do GPS:
GP-808G | BS-708 | GP-20U7
- Update rate: 1Hz | • Update rate: 1Hz-10Hz | • Update rate: 1Hz
- Comunicação UART/I
2C | • Comunicação USB 2.0 | • Comunicação UART
- 40mA @ 3.3V-5.0V | • 65mA @ 5.0V | • 40mA @ 3.3V
- Preço: 35 − 40€ | • Preço: ≈ 20€ | • Preço: 15 − 20€
- 52mm * 52mm * 20.5mm | • 56mm diametro * 18mm | • 18.4mm * 18.4mm * 4mm
- Precisão 2.5m | • Precisão 2.0m | • Precisão 2.5m
- 72 Canais | • 56 Canais | • 56 Canais

Para além do GPS, que pertence aos EUA, existe um sistema de navegação global chamado GNSS que combina constelações de satélites americanas, russas, europeias e chinesas. A principal vantagem do GNSS é que os recetores deste tipo são capazes de receber e interpretar sinais de um maior conjunto de satélites, o que melhora a qualidade dos resultados.
Os módulos acima apresentados são relativamente acessíveis, no entanto oferecem pouca precisão nos dados, sendo que retornam a posição num raio de 2.5m da localização real do objeto. Estas imprecisões podem mostrar-se desfavoráveis, já que não permitem determinar com exatidão o trajeto da mota e, consequentemente, tornar-se-ia impossível caracterizar a performance ao longo da pista (por exemplo a posição da mota numa curva). Além disso, resultados imprecisos

na posição põem em causa a alternativa anteriormente considerada de medir a velocidade através do GPS.
Para resolver este problema, podemos optar por considerar os seguintes módulos GNSS de

14 alta-precisão, que oferecem melhores resultados mas a um custo bem mais elevado:

ZED-Z9P RTK | ZED-Z9H | NEO-M8P
- Update rate: até 20Hz | • Update rate: até 10Hz | • Update rate: até 8Hz
- UART/SPI/I
2C/USB | • UART/SPI/I
| 2C/USB | • UART/SPI/I 2C/DDC
- 68mA @ 3.0V | • 68mA @ 3.0V | • 25 mA @ 3.0 V
- Preço: ≈ 190€ | • Preço: ≈ 180€ | • Preço: ≈ 150€
- 22mm*17mm*2.4mm | • 22mm*17mm*2.4mm | • 12.2mm*16mm*2.4mm
- Precisão 0.01m | • Precisão 0.01m | • Precisão 0.025m
- 184 Canais | • 184 Canais | • 72 Canais

## 4 Direção

Esta secção tem como objetivo medir o ângulo que o guiador faz com o quadro da mota. Isto permite monitorizar o manuseamento do guiador perante curvas de diferentes intensidades e, eventualmente, observar os efeitos que esse parâmetro possa ter na estrutura da mota.
Para exercer esta tarefa, destacam-se dois tipos de sensores electromecânicos bastante simples, o potenciómetro analógico e o encoder rotativo incremental. Os potenciómetros são bastante conhecidos, pois são bem comuns em vários aparelhos eletrónicos. Consiste num arco feito de um material resistivo que liga os terminais de alimentação e um cursor (Wiper ) que está em

contacto com esse arco em posições variáveis. Dependendo da posição do cursor, a resistência entre o terminal do Wiper e o ground varia e, consequentemente, a queda de tensão também varia. Por outras palavras, determina-se o ângulo do potenciómetro através do valor de tensão que ele retorna.

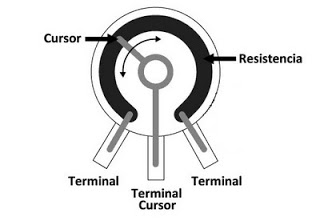
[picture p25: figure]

Figura 12: Potenciómetro Analógico Rotativo

15

Já o encoder incremental, tem um funcionamento semelhante ao descrito na secção 1 mas enquanto que o anterior tinha como objetivo medir velocidade, este pretende caracterizar o movimento e o ângulo de rotação de forma bem mais precisa.
No potenciómetro, o ângulo é dado por uma tensão elétrica e portanto, a precisão dos resultados está maioritariamente dependente da precisão do ADC do microcontrolador. Tendo em conta que os ADCs presentes nos núcleos STM32 usados são de 12 bits (0 a 4095), o que é mais

que suficiente. A precisão do encoder depende do número de fendas no disco e é geralmente expressa em pulsos por rotação (PPR). Podem-se adquirir encoders desde 100ppr, o que daria

erros relativamente grandes, até precisões na ordem dos 10000ppr, que se traduz em cerca de 0.036◦ por cada pulso (talvez seja demasiado). Portanto é uma questão de ver qual será o tipo

de encoder que mais se adequa para esta finalidade.
Geralmente, os potenciómetros analógicos têm uma liberdade de rotação limitada, não podendo dar uma volta completa. Em contraste, o encoder pode girar indefinidamente. No entanto, como o objetivo é apenas determinar o ângulo do guiador, não será um problema, já que esse ângulo tem uma amplitude relativamente reduzida.
Enquanto que no potenciómetro o valor correspondente à direção pode ser extraído através da medição do ADC e posteriormente convertido para um ângulo, o encoder precisaria de recorrer a interrupções e determinar um incremento/decremento da posição. Para além disso, o encoder necessitaria analisar dois sinais de saída (sinais A e B) de modo a poder identificar o sentido

do movimento do guiador. Ou seja, o potenciómetro permite recolher o ângulo de forma quase direta, enquanto que com o encoder é preciso determinar a variação do ângulo em relação ao instante anterior. Assim, conclui-se que, quanto à complexidade das implementações dos sensores, o potenciómetro seria a solução mais fácil, embora sejam ambas relativamente simples.
Algo que se deve ter em conta, é que como o encoder apenas consegue detetar a variação do ângulo de rotação, significa que para conhecer a direção do guiador é necessário saber o valor inicial desse ângulo. Isto exigiria que fosse feita uma calibração da direção cada vez o Low Voltage System fosse ligado para determinar a origem (0◦
). O mesmo não aconteceria com um

potenciómetro porque cada valor de saída corresponde sempre à mesma posição do cursor. Posto isto, o potenciómetro parece ser a escolha indicada para medir a direção.
Embora este seja um sensor pequeno, seria necessário arranjar uma forma não invasiva de o introduzir no protótipo. Cabe a outras áreas decidir se vale a pena e, se sim, construir uma pequena estrutura para o implementar.

16

## 5 Travel das Suspensões

Para ter uma noção da performance do amortecimento da mota durante os treinos e corridas, há que medir o travel das suspensões de modo a poder analisar como este varia. Para além disso, como a suspensão é ajustável, poderá ser útil conhecer o seu comportamento perante os vários parâmetros de modo obter o amortecimento ideal de acordo com a pista e o piloto.
Como o travel se traduz num deslocamento causado pela compressão/alongamento de molas,

sugere-se o uso de um potenciómetro linear. Este, em contraste com o potenciómetro rotativo, permite-nos medir a posição do cursor segundo uma única direção. Algumas empresas fabricam potenciómetros lineares com foco nos desportos motorizados, feitos propositadamente para medir este parâmetro. Este tipo de potenciómetro é também chamado potenciómetro de suspensão ou damper potentiometer, já que é desenhado para o efeito. E ainda necessário ter em conta o tipo ´

de encaixe que se pretende, que está dependente da estrutura dos amortecedores que serão usados na TLM04e.

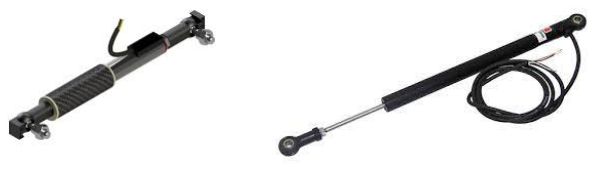
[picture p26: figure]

(a) (b)

Figura 13

Mais uma vez, a precisão das medições obtidas depende da capacidade de leitura de tensões elétricas por parte das portas analógicas do MCU que, no caso, retorna um valor digital de 12 bits após a conversão no ADC.
Para escolher o produto a adquirir, há que ter em conta o comprimento da distensão máxima prevista nas suspensões. Geralmente, a maioria das motas usa potenciómetros de 150mm na suspensão dianteira e de 75mm na traseira. Não deixa também de ser bastante importante conhecer a distância entre os encaixes das suspensões.
Quanto às ligações elétricas, o potenciómetro linear apresenta 3 pins, sendo dois deles os potenciais de referência e o terceiro é o wiper, que contém o potencial variante e que nos permite obter o valor do travel. Os conectores usados são geralmente do tipo 4 way Binder 719, que usam 4 pins, um dos quais está desconectado. è preciso um conector fêmea e um conector macho, que ficariam respetivamente na placa de telemetria e no cabo do potenciómetro, por exemplo.

17

(a) Potenciómetro na

suspensão dianteira

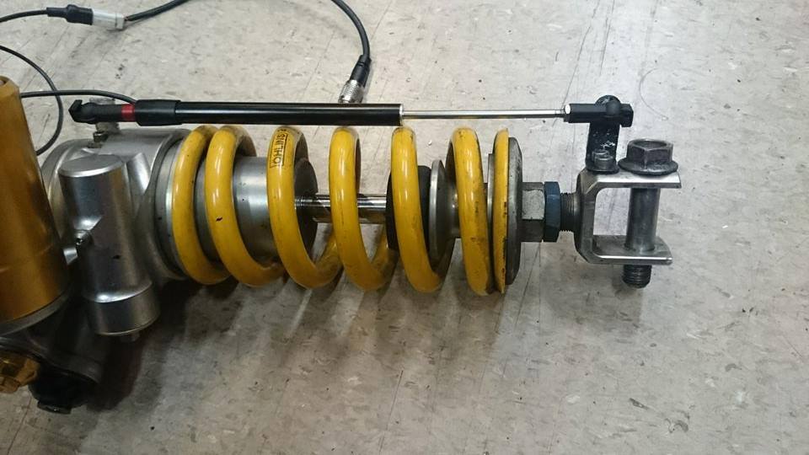
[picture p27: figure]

(b) Potenciómetro na suspensão traseira

Figura 14

Para os potenciómetros dianteiros, apresentam-se as seguintes sugestões:
| CLP-150 | SUS-POT-150-RJ | MoTeC 57155
Travel | • 150mm | • 150mm | • 150mm
Comp. fechado | • 298mm | • 229mm | • 297mm
Resistência (±20%) | • 10kΩ | • 10kΩ | • 10kΩ
Preço | • ≈ 400€ | • ≈ 225€ | • ≈ 290€

E para os potenciómetros das suspensões traseiras:
| CLP-75 | SUS-POT-75-RJ | MoTeC 57154
Travel | • 75mm | • 75mm | • 75mm
Comp. fechado | • 222mm | • 148mm | • 222mm
Resistência (±20%) | • 5kΩ | • 5kΩ | • 5kΩ
Preço | • ≈ 400€ | • ≈ 225€ | • ≈ 290€

18

## 6 Temperatura do Controlador e do Motor

Por motivos de segurança e para salvaguardar a integridade do controlador e do motor, é necessário monitorizar a temperatura neles observada. Caso a temperatura exceda valores demasiado elevados, pode ocorrer o risco de causar danos nestes equipamentos e, portanto, devem ser implementadas medidas para o evitar. Algumas dessas medidas passam por diminuir a potência elétrica fornecida ao motor, reduzir o torque exigido ou, caso necessário, desligar a alimentação do próprio controlador, quer seja internamente quer pelo contactor do High Voltage System. Esta última é análoga ao BMS, mas muitos controladores já vêm com esta proteção. O mais comum no que toca a medir temperaturas é o uso de termistores, que não são mais que semicondutores cuja resistência varia de certa com o aumento da temperatura. As principais vantagens dos termistores são o facto de serem pequenos, baratos e oferecerem boas estimativas para o valor da temperatura. Uma outra vantagem é a simplicidade da montagem, já que apenas é preciso uma outra resistência em série.

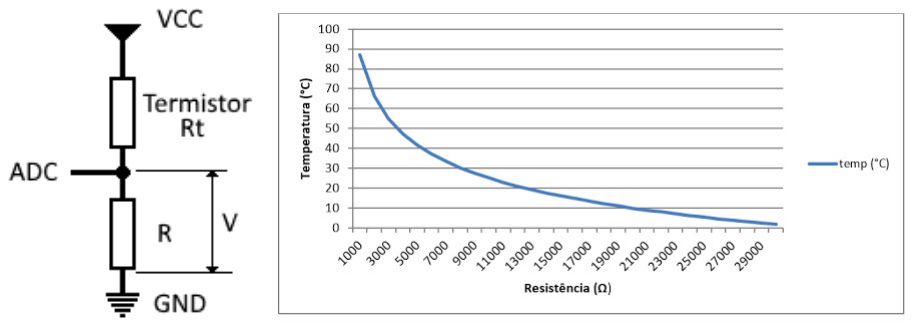
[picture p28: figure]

(a) Montagem de um termistor | (b) Temperatura em função da resistência (NTC)

Figura 15

Há também a possibilidade de medir temperatura através de infravermelhos sem precisar de contacto mas, para além de que a sua instalação na mota se tornasse mais desafiante, apenas se conseguiria medir a temperatura da superfície exterior do equipamento. Logo, podemos descartar esta opção.
Sendo a temperatura um fator importante, na maioria dos casos, tanto o motor como o controlador já contém termistores internos para este efeito. O próprio motor indica a temperatura do seu interior a através dos dados de feedback. Esse valor é obtido com um termistor, geralmente do género KTY 84 ou KTY 83 e do tipo PTC, significando que a sua resistência aumenta com o aumento da temperatura. O terminal associado à temperatura do motor é de seguida usado como input no controlador para que o seu valor seja monitorizado.
Em termos de telemetria, caso se pretenda registar a temperatura do motor, seria possível

19 obter o seu valor digitalmente através do protocolo de comunicação CAN pelo qual o controlador se rege. Por exemplo, para o controlador Sevcon Gen4 usado na TLM02e, o valor estimado a partir do termistor do motor pode ser encontrado no endereço 0x4621. Quanto à temperatura do próprio controlador, este geralmente faz a leitura térmica no heatsink, cujo valor pode também ser extraído a partir do CAN (endereço 0x5100, pelo exemplo anterior).

## 7 Inclinação da Mota

Para determinar a inclinação da mota será necessário um giroscópio, que reage à rotação angular devido à força Coriolis resultante da aceleração rotativa. A força de Coriolis é uma força fictícia que atua sobre uma massa em movimento quando fica sujeita a uma rotação. Medindo a ação desta, é possível determinar a variação do ângulo segundo um referencial de inércia. Existem diversos tipos de giroscópio, como por exemplo os giroscópios óticos, de fibra ótica, de rotor giratório e os giroscópios MEMS. Este último apresenta vantagens em relação aos anteriores por ser extremamente compacto, preciso e, principalmente, porque funciona de forma semelhante ao acelerómetro anteriormente considerado. Como já mencionado na secção 2, os módulos IMU (Inertial Measurement Unit) incluem geralmente tanto acelerómetro como giroscópio, e por vezes

magnetómetro. Posto isto, os produtos sugeridos para a medição da aceleração linear servem também para medir a inclinação da mota.

(a) Efeito Coriolis
(b) Mecanismo MEMS

Figura 16

20

## 8 Pitch

O pitch é um dos três graus de liberdade de rotação tridimensional de um corpo, juntamente com os movimentos de yaw e roll. Embora estes termos sejam maioritariamente usados na aviação e aeronáutica, também têm grande utilidade no motociclismo. A diferença mais significante é que, enquanto que aviões e foguetões rodam sobre o seu centro de massa, uma mota roda em torno dos pontos de contacto entre os pneus e o chão, descrevendo movimento completamente diferentes. O pitch traduz-se na rotação em volta do eixo horizontal transversal, correspondendo a uma inclinação para trás (”wheelie”) ou para a frente (”stoppie”) apoiando-se numa das rodas.

Como o pitch caracteriza uma inclinação, o seu valor pode também ser obtido através de um IMU. De facto, tal como mencionado na secção anterior, o módulo selecionado para o IMU será responsável por parametrizar tanto a inclinação da mota nos 3 eixos, como as acelerações a que esta está sujeita.
Esta rotação pode no entanto estar associada a movimentos mais repentinos, fazendo com que a aceleração tangencial interfira com a obtenção do ângulo de inclinação. Outro aspeto a ter em consideração na recolha dos dados é a contribuição das vibrações que atuam sobre a mota. Para lidar estes problemas há que tratar cuidadosamente os dados e combinar os acelerómetros e os giroscópios presentes no IMU. Existem algoritmos que podem ajudar no tratamento e interpretação das medições. Isto também se aplica à inclinação lateral da mota (roll).

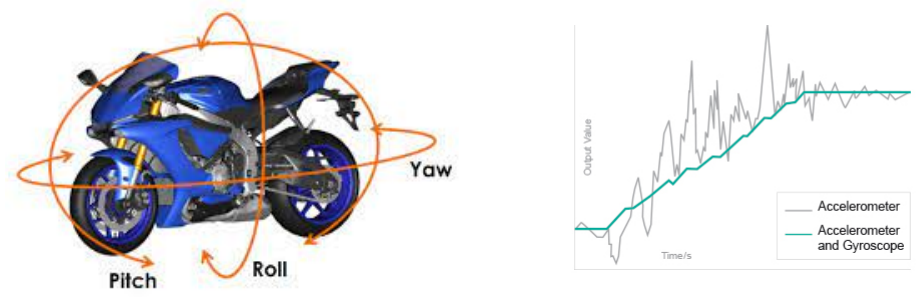
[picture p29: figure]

Figura 17

21

## 9 Rotação do Motor

Um outro parâmetro importante a ter em consideração é a velocidade de rotação do veio do motor. A monitorização do número de rotações por minuto (RPM) observadas no motor pode

ajudar a melhor compreender o desempenho do protótipo durante o funcionamento, bem como o seu comportamento perante certas partes da pista.
A primeira abordagem para obter o valor de RPM seria medir essa grandeza diretamente a partir do próprio motor. Certos motores elétricos incluem sensores internos capazes de medir a velocidade do veio, enquanto que outros podem incluir conexões que permitem ao utilizador adicionar sensores como um encoder ou um tacómetro para o efeito. O motor utilizado na TLM04e será selecionado e fornecido pela competição, logo esta solução dependerá do produto escolhido.
A segunda abordagem seria determinar a velocidade rotação através do barramento de comunicação CAN, a partir do controlador. Como o controlador é responsável pela gestão do motor, este define a velocidade mecânica que daí resulta. A potência mecânica que um motor de indução trifásico oferece depende dos parâmetros da alimentação AC, mas é fortemente influenciada pela carga mecânica e por perdas eletromagnéticas no estator e no rotor. Com a frequência da corrente fornecida pelo controlador, pode-se calcular a velocidade do campo girante (chamada velocidade de sincronismo) e, dividindo pelo número de pares de polos (característica do motor), obtém-se a

velocidade do rotor no vazio. No entanto, essa velocidade corresponde apenas à situação de não haver carga no veio, não havendo escorregamento. No caso real, é necessário estudar o binário exigido pela mota, tendo em conta fatores como a força motriz, peso da mota e do piloto e inclinações da pista, de modo a determinar uma aproximação geral do escorregamento no motor. Esta abordagem mostra-se portanto bastante mais complicada que a anterior.
Uma terceira alternativa é calcular o número de RPM usando o valor da velocidade linear da mota. Ao contrário das motas a combustão que têm uma caixa de velocidades, a roda traseira da TLM04e está diretamente ligada ao motor através da corrente, já que a velocidade do motor é regulada pelo controlador. Isto significa que a rotação do motor e a velocidade angular da roda são diretamente proporcionais, não dependendo da ”mudança”. E de notar que, para obter ´

resultados de confiança usando este método, convém realmente medir a velocidade com base na rotação de algum elemento na mota (por exemplo com um encoder ou um Wheel Speed Sensor, como descrito na secção 1). Isto porque obter o RPM do motor a partir do GPS seria pouco

coerente.

22


Figura 18: TLM03e

## 10 Correntes de Alimentação do Motor

O motor usado no protótipo é uma máquina síncrona trifásica, cujo rotor é constituído por ímanes permanentes, enquanto que o estator cria um campo magnético girante. Neste tipo de motor, o estator é formado por vários enrolamentos ligados a uma rede trifásica. Na verdade, os enrolamentos são feitos a partir de três cabos, sendo cada um deles alimentado por uma fase diferente, e devidamente configurados para que a soma de todas as contribuições vetoriais do campo magnético em cada enrolamento dê origem a um campo girante.
Apesar de o motor consumir energia na forma de corrente alternada trifásica, este e todos os outros sistemas elétricos são alimentados pelo acumulador que é uma fonte de corrente continua. E o controlador que faz a conversão de DC para AC através de inversores trifásicos e utilizando ´

PWM (Pulse Width Modulation). Ou seja, com um sinal digital é possível descrever aproxima-

damente uma sinusóide alterando o duty cicle e invertendo o sentido da tensão. Por sua vez, cada fase do motor recebe uma tensão alternada, formando um sistema de tensões equilibradas, isto é, as três ondas têm a mesma amplitude e estão desfasadas de 120◦
. E atendendo a que as
impedâncias são iguais nas três fases do motor (cargas equilibradas), as correntes serão também

equilibradas.
O controlador é responsável por determinar a corrente necessária de acordo com o torque exigido ao motor e, por sua vez, fornecer essa corrente a cada fase.
Em termos de telemetria, interessa-nos apenas saber o valor RMS da corrente, isto é, o valor eficaz da onda. Geralmente, o próprio controlador inclui a medição interna da corrente de saída, sendo o seu valor acessível através do CAN. Caso isso não aconteça, é ainda possível calcular a corrente com base no valor RMS da tensão na linha e da impedância dos enrolamentos do estator.

23

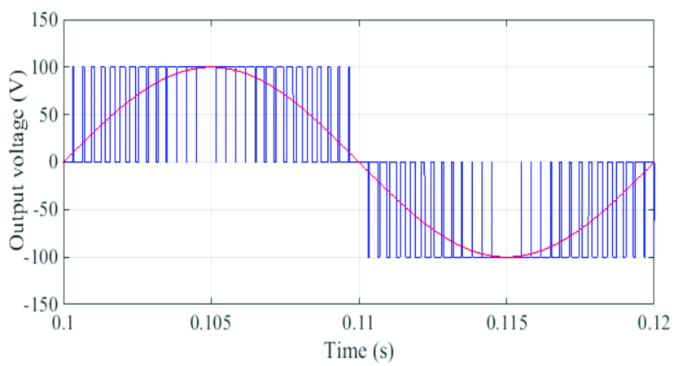
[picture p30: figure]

Figura 19: PWM

## 11 Percentagem de Acelerador e Travão

De modo a melhor compreender o comportamento da mota em resposta aos comandos do piloto, é preciso monitorizar aspetos como a aceleração e travagem, bem como a intensidade que lhes é imposta. Assim, convém determinar a razão ou percentagem associada aos controlos do

travão e do acelerador.
Quanto à aceleração, a solução torna-se bastante simples, visto que o próprio manípulo do acelerador que será usado no protótipo já consiste num potenciómetro. A maior ou menor aceleração exigida ao motor é dada pela percentagem do acelerador, cujo valor se obtém através desse potenciómetro de acordo com a amplitude de rotação imposta ao manípulo. Isto resulta num sinal analógico recebido pelo controlador, com o propósito de regular a velocidade do motor conforme a tensão desse sinal.

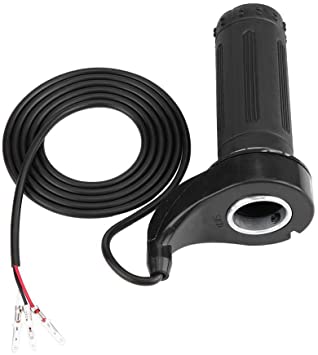
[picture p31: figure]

Figura 20: Manípulo do Acelerador

24

Para obter os valores referentes ao acelerador não é necessário, portanto, recorrer a dispositivos/sensores adicionais para além do que já foi implementado nos protótipos anteriores. Como

os três fios do potenciómetro são ligados diretamente ao controlador, uma abordagem simples seria fazer um bypass do wiper para a placa de telemetria e ler diretamente o sinal analógico com um ADC do microcontrolador. Há que ter em atenção que o potenciómetro do manípulo deve usar o mesmo Ground que o Low Voltage System, caso contrário existiria uma voltagem de offset a interferir com as medições. Um problema que poderia surgir é caso de a gama de tensões esperada no sensor não coincidir entre os instrumentos de medição. Por exemplo, enquanto o MCU espera receber valores entre os 0V e os 3.3V, alguns controladores usam voltagens dos 0V aos 10V. Neste caso, não se pode ligar diretamente os nós e, embora seja possível solucionar este problema, torna-se desnecessariamente mais complexo.
Uma outra alternativa mais elegante é utilizar os valores medidos pelo controlador, extraindo--os através do CAN. Desta forma não será necessário fazer qualquer alteração nos cabos ou no hardware para medir este parâmetro. O controlador, após interpretar o sinal analógico do wiper, converte-o para um valor digital, de por exemplo 1 byte, e de seguida envia-o para a placa de telemetria sob a forma de um inteiro de 0 a 255, a partir do qual se obtém a percentagem.
No que toca à percentagem de travagem, este parâmetro também pode ser determinado com recurso a um potenciómetro, medindo a posição da alavanca. Esse sensor pode vir também incluído no próprio travão, ou pode ter de ser incorporado à parte. O valor da percentagem pode ser obtido da mesma forma descrita no parágrafo anterior, visto que a maior parte dos controladores inclui terminais para o potenciómetro do travão. Em alternativa, poder-se-ia usar um transdutor de pressão, que é um sensor capaz de medir a pressão do óleo do travão, retornando um sinal analógico. No entanto, um potenciómetro parece ser a opção mais fiável.

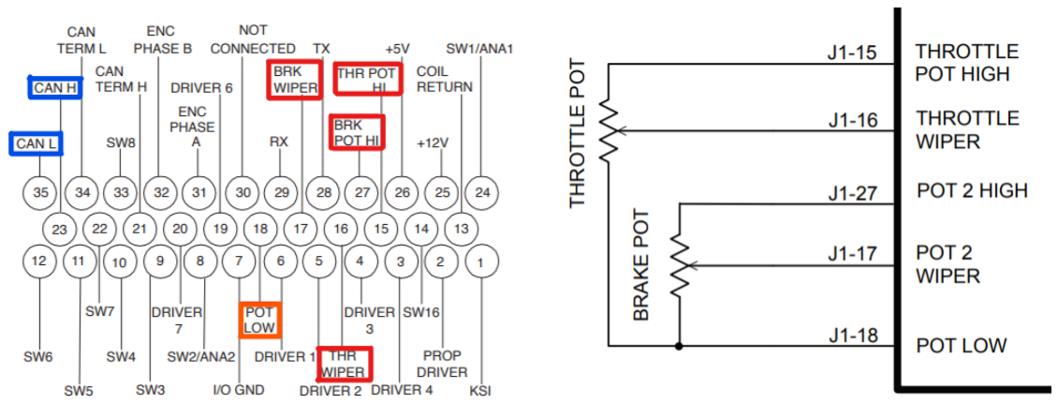
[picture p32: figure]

Figura 21: Terminais dos pot. no controlador

25

## 12 Extensómetros

Um extensómetro é um dispositivo utilizado para medir a deformação de uma estrutura a partir da variação da resistência elétrica de um condutor. Este aparelho goza da segunda lei de Ohm, R = ρ

L
A

, desprezando o alargamento da secção transversal A e considerando que a resistividade ρ do material é insensível à deformação. Assim verifica-se uma relação praticamente

linear entre a variação da resistência e a variação do comprimento do condutor.
Com o objetivo de minimizar o efeito da extensão lateral vista pelo extensómetro, este dispositivo é construído com a forma mostrada na figura 22, tornando-o quase indiferente às forças transversais que atuarem na estrutura, mas sensível a deformações longitudinais. Isto é importante pois permite-nos focar em cada componente direcional das forças a que o objeto está sujeito. Este sensor vem geralmente incorporado numa película adesiva para assegurar que o condutor sofre as mesmas tensões que a estrutura.

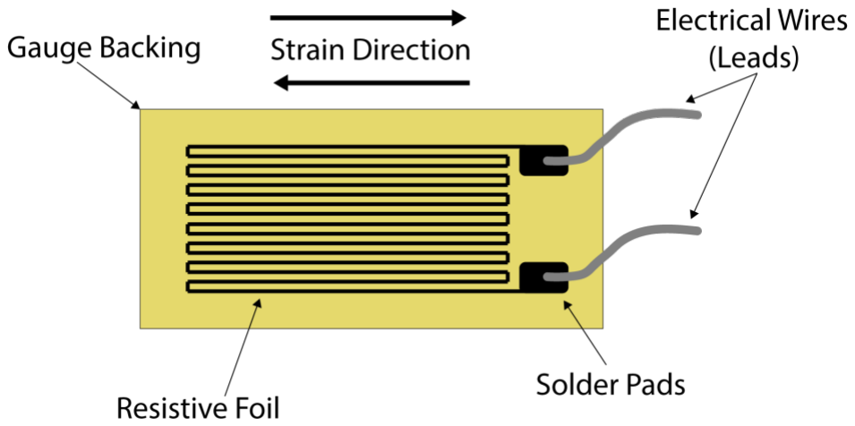
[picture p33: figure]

Figura 22: Extensómetro Elétrico

A variação da resistência sentida por um extensómetro é bastante pequena, tomando valores de ordem de grandeza entre 10⁻⁴

e 10⁻²Ω. Por este motivo, é necessário um método bastante

preciso para medir a resistência, sendo que geralmente se usa uma Ponte de Wheatstone.

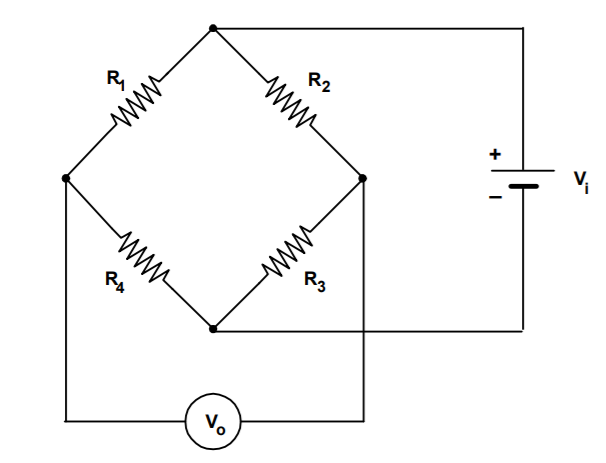
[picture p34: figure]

Figura 23: Circuito Ponte de Wheatstone

26

A seguinte tabela mostra as diferentes configurações possíveis para a implementação de extensómetros, recorrendo à ponte de Wheatstone, bem como as expressões físicas que descrevem o respetivo sinal de saída. KG é o fator de sensibilidade do extensómetro e ε diz respeito à deformação da estrutura.


Figura 24: Configurações

A configuração deve ser escolhida de acordo com o respetivo propósito e tipo de medição desejada. A tensão de entrada Vi é fixa e fornecida pela placa e a tensão de saída Vo varia perante a deformação e deve ser medida de modo a determinar essa grandeza. No entanto, visto que se trata de uma diferença de potencial relativamente baixa, o microcontrolador pode não ser capaz de fazer uma medição suficientemente precisa. Por este motivo, é necessário recorrer a outro aparelho de medida, como por exemplo um módulo Nanoshield LoadCell, que consiste num

27 shield que inclui um amplificador, filtro e um ADC de 20 bits para obter uma alta resolução. Quanto ao preço de um extensómetro, os valores podem variar bastante com o fabricante, precisão, compensação de temperatura, entre outros, mas é geralmente um produto bastante caro, rondando entre 100€ e 200€. Por exemplo, os modelos da série LY4x que funcionam apenas numa direção (idênticos ao da figura 22) custam à volta de 105€. Já modelos da série

VY4x que apresentam 4 extensómetros formando uma ponte Wheatstone completa têm custos acima de 250€.

Para concluir, este sensor tem relativamente pouca importância para o projeto, exige hardware extra e é dispendioso, não sendo uma prioridade no protótipo.

28

## 13 Tubo de Pitot

O tubo de Pitot é um instrumento de medição capaz de medir simultaneamente a pressão estática e a pressão de estagnação num fluido de forma a poder determinar a velocidade do fluxo do mesmo. Este dispositivo é, geralmente, utilizado em modelos físicos em laboratório, em redes de abastecimento de água, na medição de caudais e, principalmente, na medição da velocidade de aviões. Relativamente à TLM04e, serviria o propósito de estimar a velocidade do vento de modo a ter uma ideia do seu impacto na performance da mota.
Como foi dito anteriormente, um tubo de Pitot funciona através de medições de dois tipos de pressão. O aparelho consiste num tubo instalado paralelamente ao vento relativo e com um orifício voltado diretamente para o fluxo de ar, o que lhe permite aferir a pressão total (também chamada de pressão de estagnação). Em seguida, compara esse valor com a pressão estática, que

não é afetada pela velocidade da mota. No uso deste dispositivo em aeronaves, a pressão estática é um parâmetro que varia muito consoante a altitude, no entanto, no nosso caso, a pressão à superfície terrestre é bastante uniforme (estando apenas sujeita a condições climáticas, que têm pouco peso nesse valor). Segundo a equação de Bernoulli da Mecânica dos fluidos, a pressão total

é igual à soma da pressão estática com a pressão dinâmica, estando essa última dependente da velocidade do fluxo.


Figura 25: Tubo de Pitot

A implementação de um tubo de Pitot numa mota pode, no entanto, gerar medições pouco precisas ou até enganadoras dependendo do lugar onde é instalado. O dispositivo deve ser colocado numa zona onde o ar não sofra grandes perturbações causadas pelo deslocamento da mota. Um exemplo análogo é visto em alguns carros de Formula 1 que usam tubos de Pitot pelos mesmos motivos e os mesmos são colocados no topo de uma viga para que a medição não seja afetada pelo próprio movimento do carro no ar. Contudo, no caso de um motociclo, as opções são bastante mais escassas.

29


Figura 26: Tubo de Pitot num Formula 1

A forma mais simples e compacta de implementar este sensor é comprar um conjunto que inclui um tubo de Pitot e um digital airspeed sensor, que estão ligados através de duas intubações. O airspeed sensor é responsável por determinar a diferença de pressão e, de seguida, retorna um sinal analógico proporcional à pressão dinâmica do fluxo de ar. Existem opções que usam I2C (CUAV, Holybro, Matek 4525DO, mRobotics, Qiotek 5033, Matek DLVR), enquanto outras utilizam o protocolo UAVCAN (Matek UAVCAN DLVR, Qiotek UAVCAN 5033). O conjunto com sensor e tubo pode custar à volta de 70€.


Figura 27: Tubo de Pitot e AirSpeed Sensor

30

## Fontes

Velocidade

MDPI; (https://www.mdpi.com/2076-3417/9/3/452/htm) Motion Control Tips; (https://www.motioncontroltips.com/how-are-encoders-used-for-speed-measurement/) Apogee Web; (https://www.apogeeweb.net/article/22.html) Embedded Related; (https://www.embeddedrelated.com/showarticle/158.php9) Arduino (https://create.arduino.cc/projecthub/mitov/measure-motor-speed-rpm-with-optocoupler-and-encoder-disk-c3a0e49)

Aceleração

McLaren; (https://www.mclaren.com/applied/case-study/motogp/) American Piezo; (https://www.americanpiezo.com/piezo-theory/piezo-accelerometer.html) MEMS Exchange; (https://www.mems-exchange.org/MEMS/what-is.html) Sparkfun; (https://learn.sparkfun.com/tutorials/accelerometer-basics/all) Science Direct; (https://www.sciencedirect.com/topics/medicine-and-dentistry/accelerometer) ST; (https://www.st.com/en/mems-and-sensors/accelerometers.html) BoxRepsol (https://www.boxrepsol.com/en/motogp-en/how-do-sensors-and-electronics-improve-performance-in-motogp/)

GPS

Engineers Garage; (https://www.engineersgarage.com/featured/gps-basics-ublox-skytraq-sirf/) Sparkfun GPS Basics; (https://learn.sparkfun.com/tutorials/gps-basics/all) Sparkfun Fundamentals; (https://cdn.sparkfun.com/datasheets/Sensors/GPS/fundamentals_of_gps_receivers-v1.pdf) Sparkfun GPS Mouse; (https://learn.sparkfun.com/tutorials/gps-mouse---gp-808g-hookup-guide/all) Wikipedia NMEA; (https://en.wikipedia.org/wiki/NMEA_0183) Artigo sobre EMI; (http://davidlu.net/13869667.pdf) Sparkfun GNSS; (https://cdn.sparkfun.com/assets/learn_tutorials/5/7/1/GPM-808G--UAV_GNSS_receiver_ublox8030_QMC5883.pdf) GPS World; (https://www.gpsworld.com/commentary-high-precision-positioning-is-going-mainstream/) GNSS OEM (https://www.gnss.store/17-high-precision-gnss-modules)

Direção

Squids Arduino; (http://www.squids.com.br/arduino/index.php/hardware/componentes-eletronicos/75-potenciometro) Thomson Linear Motion; (https://www.thomsonlinear.com/pt/suporte/dicas/que-tipos-de-potenciometros-usamos-em-nossos-atuadores-e-como-funcionam) Bóson Treinamentos; (http://www.bosontreinamentos.com.br/eletronica/curso-de-eletronica/como-funciona-um-potenciometro/) HI Tecnologia; (https://www.hitecnologia.com.br/blog/o-que-%C3%A9-encoder-para-que-serve-como-escolher-como-interfacear/) Dynapar (https://www.dynaparencoders.com.br/blog/resolucao-do-encoder-precisao-do-encoder-e-repetibilidade-do-sistema/)

Travel das Suspenções

dataMC; (https://www.datamc.org/data-acquisition/adding-sensors/suspension-potentiometers/) FSAE; (http://www.fsae.com/forums/showthread.php?5776-Mounting-damper-travel-sensors) KA Sensors; (https://www.kasensors.com/en/products/position) AiM Shop (https://www.aimshop.com/products/aim-car-suspension-potentiometer-with-pop-end-fitting)

Inclinação da Mota

Unicentro; (https://www3.unicentro.br/petfisica/2018/09/11/efeito-coriolis/) Artigo ”Roll Angle Estimation for Motorcycles”; (https://www.researchgate.net/publication/228117316_Roll_Angle_Estimation_for_Motorcycles_Comparing_Video_and_Inertial_Sensor_Approaches) Artigo ”Real-Time Roll Angle Estimation for Two-Wheeled Vehicles” (https://www.researchgate.net/publication/261834546_Real-Time_Roll_Angle_Estimation_for_Two-Wheeled_Vehicles)

Pitch

Motorcyclist; (https://www.motorcyclistonline.com/blogs/roll-pitch-and-yaw-drawing-line/) Artigo ”Derivation of a pitch angle value for the motorcycle”; (https://link.springer.com/content/pdf/10.1140/epjst/e2020-900278-4.pdf) Springer Link (https://link.springer.com/article/10.1140/epjst/e2020-900278-4)

Informações sobre Controladores

Manual Sevcon Gen 4; (https://www.thunderstruck-ev.com/images/Gen4%20Product%20Manual%20V3%204.pdf) Documentação CURTIS 1239; (https://www.hpevs.com/Site/images/jpeg/documentation/1239/econtroller_532_up/auto1239_Controller_532_revA_6-9-17.pdf) Spec. Sheet CURTIS 1239; (https://cdn.shopify.com/s/files/1/1820/0269/files/Curtis_1239_E_spec_sheet.pdf?2088683796436462471) EV West (https://www.evwest.com/catalog/product_info.php?products_id=230)

Informações sobre Motores

Datasheet Engiro 205A-04010-ABC (https://www.engiro.de/fileadmin/pdfs/Datenblaetter_engiro/205A/ENGIRO_Datasheet_205A_04010_ABC_V001.pdf)

Extensómetros

Artigo ”Extensômetros Elétricos”; (https://sistemas.eel.usp.br/docentes/arquivos/5840793/LOM3086/Extensometros_eletricos.pdf) HBM (https://www.hbm.com/en/7163/wheatstone-bridge-circuit/)

31

Tubos de Pitot

Projeto ”Tubo de Pitot” (UNESP); (https://www.sorocaba.unesp.br/Home/Extensao/Engenhocas/projeto-tubo-de-pitot.pdf) Cultura Aeronáutica; (http://culturaaeronautica.blogspot.com/2011/04/tubo-de-pitot-como-funciona.html) Slides Universidade de Coimbra; (https://www.eq.uc.pt/~lferreira/BIBL_SEM/global/pitot/PDF/pitot.pdf)

Auto123 (https://www.auto123.com/en/racing-news/f1-technique-measuring-air-speed-with-pitot-tubes?artid=173220)


32

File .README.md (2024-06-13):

# Telemetry System for TLM03e and TLM04e

title

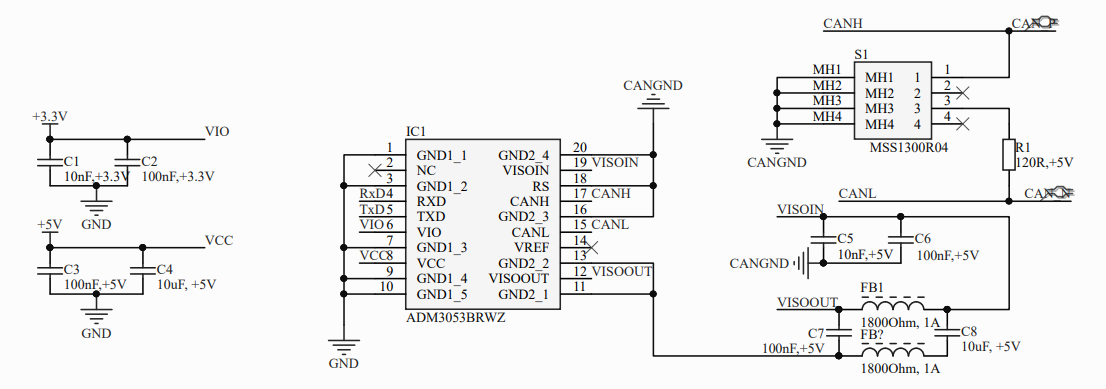
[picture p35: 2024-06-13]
telemetry-PCB/can transciever.PNG

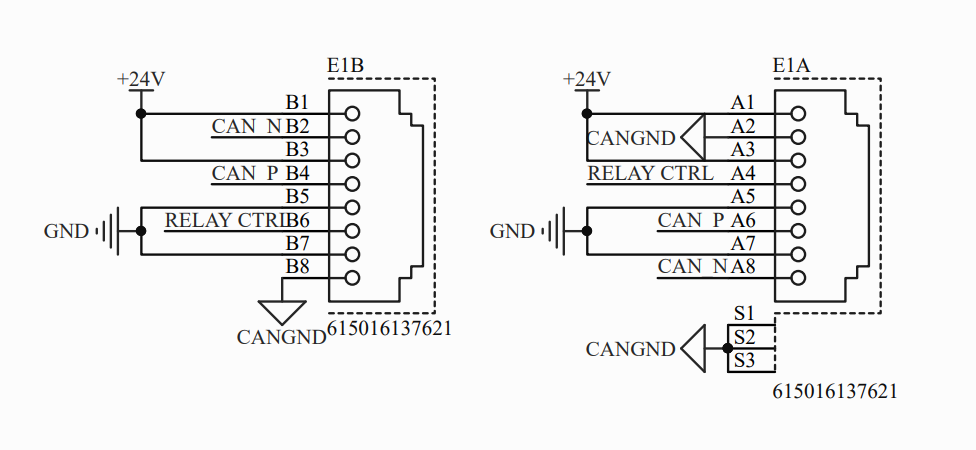
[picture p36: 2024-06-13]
telemetry-PCB/can connection.PNG

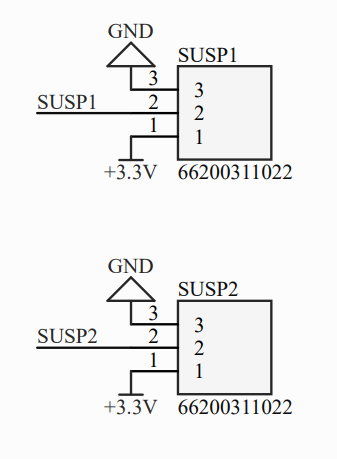
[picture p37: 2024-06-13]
telemetry-PCB/susps.PNG

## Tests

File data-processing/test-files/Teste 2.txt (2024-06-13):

susp 1022,1065,19998 
susp 1041,1016,20098 
susp 1019,1054,20198 
susp 1002,1043,20298 
susp 1006,1033,20398 
susp 1014,1053,20498 
susp 1065,1014,20598 
susp 1021,1060,20698 
susp 1013,1046,20798 
susp 1006,1028,20898 
susp 1029,1030,20998 
susp 1047,1004,21098 
susp 1037,995,21198 
susp 1018,1052,21298 
susp 1056,1012,21398 
susp 1004,1051,21498 
susp 1074,1023,21598 
susp 1044,991,21698 
susp 1066,1020,21798 
susp 992,1040,21898 
susp 1003,1044,21998 
susp 1020,1059,22098 
susp 1041,1002,22198 
susp 1053,1021,22298 
susp 1029,1030,22398 
susp 1025,1066,22498 
susp 1052,1010,22598 
susp 1035,995,22698 
susp 1041,1039,22798 
susp 996,1041,22898 
susp 1053,1012,22998 
susp 989,1034,23098 
susp 1009,1049,23198 
susp 1033,1030,23298 
susp 1009,1051,23398 
susp 1008,1056,23498 
susp 1011,1056,23598 
susp 1054,1015,23698 
susp 1039,991,23798 
susp 1048,1009,23898 
susp 1050,1020,23998 
susp 1001,1043,24098 
susp 1008,1034,24198 
susp 1000,1049,24298 
susp 1004,1048,24398 
susp 1076,1022,24498 
susp 1046,1012,24598 
susp 1047,1012,24698 
susp 1074,1023,24798 
susp 1028,1028,24898 
susp 1064,1014,24998 
susp 1046,1017,25098 
susp 1053,1021,25198 
susp 1054,1018,25298 
susp 1018,1046,25398 
susp 1010,1056,25498 
susp 1001,1045,25598 
susp 1017,1054,25698 
susp 988,1033,25798 
susp 1038,1005,25898 
susp 1007,1056,25998 
susp 1041,996,26098 
susp 1023,1061,26198 
susp 1027,987,26298 
susp 1077,1041,26398 
susp 1061,1027,26498 
susp 1049,1003,26598 
susp 1029,1029,26698 
susp 1058,1022,26798 
susp 1066,1023,26898 
susp 999,1053,26998 
susp 1017,1065,27098 
susp 1046,1018,27198 
susp 1054,1021,27298 
susp 986,1030,27398 
susp 1043,1040,27498 
susp 1040,996,27598 
susp 1022,1063,27698 
susp 1022,1078,27798 
susp 1013,1064,27898 
susp 1075,1035,27998 
susp 1003,1050,28098 
susp 1070,1037,28198 
susp 1021,1071,28298 
susp 1019,1063,28398 
susp 1058,1020,28498 
susp 1009,1052,28598 
susp 1010,1036,28698 
susp 1000,1042,28798 
susp 1049,1003,28898 
susp 1031,1034,28998 
susp 1009,1052,29098 
susp 1017,1061,29198 
susp 1061,1025,29298 
susp 1031,1032,29398 
susp 999,1050,29498 
susp 1036,994,29598 
susp 980,1023,29698 
susp 1034,1008,29798 
susp 1020,1066,29898 
susp 1050,1004,29998 
susp 1005,1048,30098 
susp 1014,1068,30198 
susp 1048,1005,30298 
susp 1043,998,30398 
susp 1025,1013,30498 
susp 1052,1013,30598 
susp 1030,1025,30698 
susp 1019,1025,30798 
susp 1057,1020,30898 
susp 1007,1060,30998 
susp 1027,1006,31098 
susp 1017,1045,31198 
susp 1015,1026,31298 
susp 1024,1068,31398 
susp 1004,1041,31498 
susp 1031,1031,31598 
susp 1056,1007,31698 
susp 1050,1016,31798 
susp 1057,1016,31898 
susp 1020,1059,31998 
susp 1016,1053,32098 
susp 1036,1000,32198 
susp 1020,1060,32298 
susp 1064,1019,32398 
susp 1029,1047,32498 
susp 1060,1018,32598 
susp 1059,1007,32698 
susp 1016,1060,32798 
susp 1029,1030,32898 
susp 1002,1044,32998 
susp 1013,1030,33097 
susp 1015,1025,33197 
susp 1033,989,33297 
susp 1060,1013,33397 
susp 1053,1011,33497 
susp 1018,1026,33597 
susp 1056,1006,33697 
susp 1011,1056,33797 
susp 1048,1009,33897 
susp 1045,1011,33997 
susp 1012,1047,34097 
susp 1013,1025,34197 
susp 1061,1019,34297 
susp 1038,1009,34397 
susp 1052,1016,34497 
susp 1053,1011,34597 
susp 989,1040,34697 
susp 1029,1062,34797 
susp 1015,1056,34897 
susp 983,1027,34997 
susp 1020,1060,35097 
susp 1020,1055,35197 
susp 1008,1046,35297 
susp 1058,1013,35397 
susp 1020,1043,35497 
susp 1064,1014,35597 
susp 1044,1004,35697 
susp 1046,1003,35797 
susp 1056,1018,35897 
susp 1028,1068,35997 
susp 1042,1002,36097 
susp 1017,1052,36197 
susp 999,1042,36297 
susp 1023,1054,36397 
susp 1023,1059,36497 
susp 1027,1072,36597 
susp 1007,1054,36697 
susp 1022,1028,36797 
susp 1053,1017,36897 
susp 1042,1078,36997 
susp 1016,1059,37097 
susp 1023,1033,37197 
susp 1056,1012,37297 
susp 1012,1056,37397 
susp 1045,1013,37497 
susp 1030,992,37597 
susp 1010,1054,37697 
susp 1049,1015,37797 
susp 1023,1079,37897 
susp 1023,1077,37997 
susp 1013,1064,38097 
susp 1078,1043,38197 
susp 1033,1029,38297 
susp 1051,1012,38397 
susp 1052,1011,38497 
susp 1052,1014,38597 
susp 1018,1052,38697 
susp 1018,1050,38797 
susp 1048,1002,38897 
susp 1044,1003,38997 
susp 1030,1016,39097 
susp 1059,1019,39197 
susp 1009,1052,39297 
susp 1040,1033,39397 
susp 1031,1015,39497 
susp 1026,1015,39597 
susp 1045,1010,39697 
susp 1011,1056,39797 
susp 1022,1071,39897 
$GPGGA,235942.800,,,,,$GPVTG,0.00,T,,M,0.00,N,0.00,K,2745

$GPGGA,235943.800,,,,,$GPVTG,0.00,T,,M,0.00,N,0.00,K,3836

$GPGGA,235945.799,,,,,$GPVTG,0.00,T,,M,0.00,N,0.00,K,4898

$GPGGA,235946.799,,,,,$GPVTG,0.00,T,,M,0.00,N,0.00,K,6727

$GPGGA,235947.799,,,,,$GPVTG,0.00,T,,M,0.00,N,0.00,K,7807

$GPGGA,235950.800,,,,,$GPVTG,0.00,T,,M,0.00,N,0.00,K,9953

$GPGGA,235951.800,,,,,$GPVTG,0.00,T,,M,0.00,N,0.00,K,11572

$GPGGA,235952.589,,,,,$GPVTG,0.00,T,,M,0.00,N,0.00,K,12644

$GPGGA,155714.097,,,,,$GPVTG,0.00,T,,M,0.00,N,0.00,K,13722

$GPGGA,155715.097,,,,,$GPVTG,0.00,T,,M,0.00,N,0.00,K,14788

$GPGGA,155716.097,,,,,$GPVTG,0.00,T,,M,0.00,N,0.00,K,16617

$GPGGA,155719.097,,,,,$GPVTG,0.00,T,,M,0.00,N,0.00,K,18765

$GPGGA,155720.097,,,,,$GPVTG,0.00,T,,M,0.00,N,0.00,K,20595

$GPGGA,155721.097,,,,,$GPVTG,0.00,T,,M,0.00,N,0.00,K,21673

$GPGGA,155724.097,,,,,$GPVTG,0.00,T,,M,0.00,N,0.00,K,23821

$GPGGA,155725.097,,,,,$GPVTG,0.00,T,,M,0.00,N,0.00,K,25658

$GPGGA,155726.097,,,,,$GPVTG,0.00,T,,M,0.00,N,0.00,K,26714

$GPGGA,155728.097,,,,,$GPVTG,0.00,T,,M,0.00,N,0.00,K,27804

$GPGGA,155729.097,,,,,$GPVTG,0.00,T,,M,0.00,N,0.00,K,28860

$GPGGA,155730.092,,,,,$GPVTG,209.38,T,,M,0.07,N,0.13,K,30642

$GPGGA,155731.092,3844.2586,N,00908.2268,W,$GPVTG,234.61,T,,M,0.10,N,0.18,K,30956

$GPGGA,155733.000,3844.2587,N,00908.2266,W,$GPVTG,141.09,T,,M,0.06,N,0.11,K,32774

$GPGGA,155734.000,3844.2588,N,00908.2265,W,$GPVTG,181.73,T,,M,0.15,N,0.28,K,33684

$GPGGA,155736.000,3844.2588,N,00908.2262,W,$GPVTG,224.11,T,,M,0.08,N,0.15,K,35835

$GPGGA,155737.000,3844.2589,N,00908.2261,W,$GPVTG,290.51,T,,M,0.10,N,0.18,K,36772

$GPGGA,155738.000,3844.2590,N,00908.2259,W,$GPVTG,254.59,T,,M,0.10,N,0.19,K,37672

$GPGGA,155740.000,3844.2592,N,00908.2258,W,$GPVTG,221.21,T,,M,0.09,N,0.16,K,39839

$GPGGA,155741.000,3844.2593,N,00908.2257,W,$GPVTG,279.43,T,,M,0.07,N,0.12,K,40757

$GPGGA,155742.000,,$GPVTG,221.85,T,,M,0.11,N,0.21,K,41664

$GPGGA,155743.000,3844.2592,N,00908.2255,W,$GPVTG,176.39,T,,M,0.12,N,0.22,K,42895

susp 1011,1053,39997 
susp 1063,1031,40097 
susp 998,1046,40197 
susp 1040,993,40297 
susp 1016,1057,40397 
susp 1052,1010,40497 
susp 1046,1008,40597 
susp 1017,1044,40697 
susp 1067,1028,40797 
susp 1061,1032,40897 
susp 1050,1009,40997 
susp 1010,1043,41097 
susp 1064,1018,41197 
susp 1035,1032,41297 
susp 1053,1016,41397 
susp 1017,1061,41497 
susp 1040,1000,41597 
susp 1036,996,41697 
susp 1063,1031,41797 
susp 1033,988,41897 
susp 1021,1057,41997 
susp 1061,1027,42097 
susp 1018,1053,42197 
susp 1066,1024,42297 
susp 1002,1044,42397 
susp 1023,1077,42497 
susp 1010,1041,42597 
susp 1009,1047,42697 
susp 1049,1009,42797 
susp 1017,1041,42897 
susp 1033,1025,42997 
susp 1017,1064,43097 
susp 1047,1016,43197 
susp 1064,1022,43297 
susp 1041,1035,43397 
susp 1037,1003,43497 
susp 1042,1001,43597 
susp 1076,1022,43697 
susp 1010,1029,43797 
susp 1039,1001,43897 
susp 1047,1020,43997 
susp 1011,1029,44097 
susp 1069,1015,44197 
susp 1001,1041,44297 
susp 1023,1061,44397 
susp 1035,1030,44497 
susp 1057,1018,44597 
susp 1013,1052,44697 
susp 1025,1055,44797 
susp 1032,994,44897 
susp 1050,1007,44997 
susp 1001,1031,45097 
susp 1057,1012,45197 
susp 1016,1059,45297 
susp 1025,1068,45397 
susp 1043,1005,45497 
susp 1053,1007,45597 
susp 1067,1015,45697 
susp 1066,1020,45797 
susp 1025,1073,45897 
susp 1015,1031,45997 
susp 1012,1057,46097 
susp 1014,1059,46197 
susp 996,1035,46297 
susp 1006,1049,46397 
susp 1038,1000,46497 
susp 1012,1034,46597 
susp 998,1041,46697 
susp 1017,977,46797 
susp 1045,1005,46897 
susp 991,1035,46997 
susp 1044,1003,47097 
susp 1005,1028,47197 
susp 993,1040,47297 
susp 1022,1055,47397 
susp 1042,998,47497 
susp 1018,1036,47597 
susp 1022,1053,47697 
susp 1010,1046,47797 
susp 1036,997,47897 
susp 1038,1038,47997 
susp 1017,1060,48097 
susp 1034,1071,48197 
susp 1029,1030,48297 
susp 1051,1007,48397 
susp 1030,1021,48497 
susp 1020,1027,48597 
susp 1043,1003,48697 
susp 1019,1026,48797 
susp 1033,1001,48897 
susp 1028,1068,48996 
susp 998,1036,49096 
susp 978,1025,49196 
susp 1063,1018,49296 
susp 1067,1019,49396 
susp 1053,1007,49496 
susp 1045,1003,49596 
susp 1056,1015,49696 
susp 1049,1014,49796 
susp 1014,1065,49896 
susp 1073,1030,49996 
susp 1059,1016,50096 
susp 1049,1007,50196 
susp 1001,1040,50296 
susp 1007,1061,50396 
susp 1065,1022,50496 
susp 1043,1003,50596 
susp 1012,1059,50696 
susp 1021,1058,50796 
susp 1063,1031,50896 
susp 1008,1053,50996 
susp 1022,1059,51096 
susp 1005,1056,51196 
susp 1058,1013,51296 
susp 1000,1041,51396 
susp 1010,1050,51496 
susp 990,1040,51596 
susp 1040,1004,51696 
susp 1053,1018,51796 
susp 1056,1005,51896 
susp 1058,1013,51996 
susp 1043,1019,52096 
susp 1007,1062,52196 
susp 1004,1044,52296 
susp 1040,996,52396 
susp 1034,1008,52496 
susp 1051,1007,52596 
susp 1022,1076,52696 
susp 1027,1021,52796 
susp 1004,1053,52896 
susp 1016,1043,52996 
susp 1017,1059,53096 
susp 1016,1057,53196 
susp 1006,1058,53296 
susp 1028,1026,53396 
susp 991,1045,53496 
susp 1071,1041,53596 
susp 1018,1044,53696 
susp 1041,1011,53796 
susp 1056,1007,53896 
susp 1027,1008,53996 
susp 1026,1018,54096 
susp 1000,1033,54196 
susp 1057,1017,54296 
susp 1044,1006,54396 
susp 999,1055,54496 
susp 1046,1020,54596 
susp 1022,1072,54696 
susp 1031,1001,54796 
susp 1014,1047,54896 
susp 1010,1033,54996 
susp 1011,1056,55096 
susp 1038,1000,55196 
susp 1005,1050,55296 
susp 1012,1061,55396 
susp 1004,1050,55496 
susp 1069,1034,55596 
susp 1011,1050,55696 
susp 1004,1047,55796 
susp 1046,1006,55896 
susp 1059,1012,55996 
susp 994,1040,56096 
susp 1060,1023,56196 
susp 1036,1002,56296 
susp 1061,1014,56396 
susp 1031,1029,56496 
susp 1001,1041,56596 
susp 1046,1004,56696 
susp 1001,1044,56796 
susp 1027,994,56896 
susp 1052,1015,56996 
susp 1032,1070,57096 
susp 1004,1050,57196 
susp 1025,1028,57296 
susp 1016,1027,57396 
susp 1025,1033,57496 
susp 1043,999,57596 
susp 1053,1006,57696 
susp 1054,1007,57796 
susp 1056,1007,57896 
susp 1016,1059,57996 
susp 1014,1030,58096 
susp 1029,1035,58196 
susp 1065,1020,58296 
susp 1021,1055,58396 
susp 1013,1045,58496 
susp 1043,1011,58596 
susp 1024,1066,58696 
susp 1066,1014,58796 
susp 1017,1047,58896 
susp 1064,1015,58996 
susp 1010,1051,59096 
susp 1020,1059,59196 
susp 1040,996,59296 
susp 1024,1067,59396 
susp 1019,1065,59496 
susp 1019,1055,59596 
susp 1010,1048,59696 
susp 1046,1017,59796 
susp 1032,1035,59896 
susp 1009,1029,59996 
susp 999,1025,60096 
susp 1066,1021,60196 
susp 1054,1007,60296 
susp 1003,1042,60396 
susp 1035,1059,60496 
susp 1038,1077,60596 
susp 1023,1032,60696 
susp 1010,1057,60796 
susp 1010,1024,60896 
susp 1010,1026,60996 
susp 1007,1028,61096 
susp 1039,1000,61196 
susp 1011,1045,61296 
susp 1008,1046,61396 
susp 1057,1022,61496 
susp 1047,998,61596 
susp 1014,1056,61696 
susp 1012,1050,61796 
susp 1030,1037,61896 
susp 1013,1061,61996 
susp 1026,1023,62096 
susp 1073,1030,62196 
susp 1023,1065,62296 
susp 1013,1049,62396 
susp 986,1027,62496 
susp 1058,1016,62596 
susp 1050,1006,62696 
susp 1028,1011,62796 
susp 1027,1023,62896 
susp 1072,1033,62996 
susp 1025,1022,63096 
susp 1021,1061,63196 
susp 1036,1032,63296 
susp 1000,1042,63396 
susp 1022,1059,63496 
susp 1019,1064,63596 
susp 1049,1008,63696 
susp 1000,1040,63796 
susp 1012,1057,63896 
susp 1018,1063,63996 
susp 1056,1009,64096 
susp 1047,1013,64196 
susp 1025,1020,64296 
susp 1057,1014,64396 
susp 1005,1050,64496 
susp 1008,1053,64596 
susp 998,1050,64696 
susp 1069,1033,64796 
susp 1069,1031,64896 
susp 1069,1038,64995 
susp 1024,1014,65095 
susp 1017,1058,65195 
susp 1031,1017,65295 
susp 1067,1028,65395 
susp 1037,1014,65495 
susp 1015,1064,65595 
susp 1001,1039,65695 
susp 1019,1065,65795 
susp 1005,1056,65895 
susp 1008,1052,65995 
susp 1066,1026,66095 
susp 1012,1056,66195 
susp 1012,1059,66295 
susp 1031,1002,66395 
susp 1066,1023,66495 
susp 1028,1026,66595 
susp 1034,987,66695 
susp 1016,1062,66795 
susp 1038,1006,66895 
susp 1035,1030,66995 
susp 1028,1025,67095 
susp 1046,1013,67195 
susp 1052,1017,67295 
susp 1021,1072,67395 
susp 1059,1024,67495 
susp 1038,1004,67595 
susp 1061,1031,67695 
susp 1063,1029,67795 
susp 1046,1007,67895 
susp 1053,1020,67995 
susp 1053,1015,68095 
susp 1018,1064,68195 
susp 1001,1041,68295 
susp 1051,1005,68395 
susp 1057,1012,68495 
susp 1028,1061,68595 
susp 1035,1076,68695 
susp 1027,1069,68795 
susp 1049,1019,68895 
susp 1027,1062,68995 
susp 1055,1011,69095 
susp 1049,999,69195 
susp 1020,1047,69295 
susp 1037,996,69395 
susp 1051,1020,69495 
susp 998,1037,69595 
susp 1054,1016,69695 
susp 1054,1011,69795 
susp 1016,1025,69895 
susp 1032,1069,69995 
susp 1024,1062,70095 
susp 1000,1031,70195 
susp 1009,1051,70295 
susp 1018,1058,70395 
susp 1057,1016,70495 
susp 1018,1064,70595 
susp 996,1031,70695 
susp 1027,1063,70795 
susp 1043,1002,70895 
susp 1057,1012,70995 
susp 1009,1043,71095 
susp 1003,1044,71195 
susp 998,1042,71295 
susp 1057,1016,71395 
susp 1076,1022,71495 
susp 1027,1061,71595 
susp 1049,999,71695 
susp 1016,1053,71795 
susp 1010,1052,71895 
susp 1002,1044,71995 
susp 1044,1002,72095 
susp 1005,1044,72195 
susp 987,1033,72295 
susp 1049,1020,72395 
susp 1033,993,72495 
susp 1027,1029,72595 
susp 999,1024,72695 
susp 1015,1056,72795 
susp 1011,1058,72895 
susp 1012,1056,72995 
susp 1046,1019,73095 
susp 1058,1012,73195 
susp 1012,1050,73295 
susp 1028,1068,73395 
susp 1048,1010,73495 
susp 1028,987,73595 
susp 1049,1020,73695 
susp 1038,1031,73795 
susp 1023,1067,73895 
susp 1030,1033,73995 
susp 1038,1071,74095 
susp 999,1025,74195 
susp 1048,1005,74295 
susp 999,1042,74395 
susp 1033,1028,74495 
susp 1050,1007,74595 
susp 1015,1068,74695 
susp 1029,1030,74795 
susp 1007,1059,74895 
susp 1007,1065,74995 
susp 1006,1049,75095 
susp 1050,1011,75195 
susp 1040,1003,75295 
susp 1012,1062,75395 
susp 1020,1055,75495 
susp 1022,1074,75595 
susp 1018,1047,75695 
susp 1017,1061,75795 
susp 1014,1046,75895 
susp 1062,1028,75995 
susp 1064,1019,76095 
susp 1034,1027,76195 
susp 1003,1038,76295 
susp 1052,1013,76395 
susp 1018,1046,76495 
susp 1007,1059,76595 
susp 1017,1064,76695 
susp 1038,1008,76795 
susp 1038,1036,76895 
susp 1021,1056,76995 
susp 1020,1048,77095 
susp 1021,1034,77195 
susp 1019,1063,77295 
susp 1073,1029,77395 
susp 1008,1049,77495 
susp 1057,1013,77595 
susp 1053,1017,77695 
susp 1029,1010,77795 
susp 1058,1018,77895 
susp 1016,1060,77995 
susp 1001,1050,78095 
susp 1021,1055,78195 
susp 1023,1062,78295 
susp 1004,1039,78395 
susp 1047,1016,78495 
susp 1064,1021,78595 
susp 1011,1058,78695 
susp 999,1048,78795 
susp 1004,1042,78895 
susp 1058,1017,78995 
susp 1015,1067,79095 
susp 1054,1018,79195 
susp 1025,1018,79295 
susp 1030,1032,79395 
susp 1024,1017,79495 
susp 1026,995,79595 
susp 1002,1045,79695 
susp 1050,1011,79795 
susp 1021,1057,79895 
$GPGGA,155744.000,3844.2592,N,00908.2255,W,$GPVTG,180.02,T,,M,0.13,N,0.24,K,43809

$GPGGA,155745.000,3844.2592,N,00908.2254,W,$GPVTG,200.09,T,,M,0.15,N,0.27,K,44744

$GPGGA,155747.000,3844.2592,N,00908.2253,W,$GPVTG,295.71,T,,M,0.04,N,0.08,K,46879

$GPGGA,155748.000,3844.2593,N,00908.2252,W,$GPVTG,339.35,T,,M,0.12,N,0.22,K,47807

$GPGGA,155749.000,3844.2593,N,00908.2,$GPVTG,310.29,T,,M,0.02,N,0.04,K,48742

$GPGGA,155750.000,3844.2594,N,00908.2252,W,$GPVTG,42.13,T,,M,0.11,N,0.20,K,49960

$GPGGA,155751.000,3844.2594,N,00908.2251,W,$GPVTG,64.15,T,,M,0.12,N,0.23,K,50878

$GPGGA,155752.000,3844.2595,N,00908.2250,W,$GPVTG,16.92,T,,M,0.17,N,0.31,K,51790

$GPGGA,155753,$GPVTG,54.80,T,,M,0.08,N,0.15,K,52719

$GPGGA,155754.000,3844.2596,N,00908.2251,W,$GPVTG,264.18,T,,M,0.03,N,0.05,K,53962

$GPGGA,155755.000,3844.2596,N,00908.2251,W,$GPVTG,263.11,T,,M,0.12,N,0.21,K,54870

$GPGGA,155756.000,3844.2596,N,00908.2252,W,$GPVTG,273.78,T,,M,0.15,N,0.28,K,55785

$GPGGA,155758.000,3844.2597,N,00908.2252,W,$GPVTG,214.20,T,,M,0.12,N,0.23,K,57943

$GPGGA,155759.000,3844.2597,N,00908.2252,W,$GPVTG,181.15,T,,M,0.13,N,0.24,K,58855

$GPGGA,155800.000,3844.2597,N,00,$GPVTG,221.90,T,,M,0.13,N,0.25,K,59775

$GPGGA,155801.000,3844.2597,N,00908.2253,W,$GPVTG,194.94,T,,M,0.10,N,0.18,K,61010

$GPGGA,155802.000,3844.2597,N,00908.2253,W,$GPVTG,221.64,T,,M,0.03,N,0.05,K,61932

$GPGGA,155803.000,3844.2598,N,00908.2254,W,$GPVTG,334.55,T,,M,0.10,N,0.19,K,62858

$GPGGA,155805.000,3844.2598,N,00908.2255,W,$GPVTG,195.10,T,,M,0.02,N,0.03,K,65008

$GPGGA,155806.000,3844.2599,N,00908.2255,W,$GPVTG,344.68,T,,M,0.18,N,0.33,K,65921

$GPGGA,155807.000,3844.2599,N,00908.2255,W,$GPVTG,30.61,T,,M,0.17,N,0.31,K,66856

$GPGGA,155809.000,3844.2599,N,00908.2254,W,$GPVTG,40.68,T,,M,0.16,N,0.30,K,69023

$GPGGA,155810.000,3844.2599,N,00908.2254,W,$GPVTG,326.52,T,,M,0.11,N,0.20,K,69945

$GPGGA,155811.000,3844.25,$GPVTG,236.17,T,,M,0.05,N,0.10,K,70864

$GPGGA,155812.000,3844.2598,N,00908.2255,W,$GPVTG,228.73,T,,M,0.10,N,0.19,K,72078

$GPGGA,155813.000,3844.2599,N,00908.2255,W,$GPVTG,335.15,T,,M,0.06,N,0.11,K,72994

$GPGGA,155814.000,3844.2598,N,00908.2255,W,$GPVTG,269.59,T,,M,0.11,N,0.21,K,73908

$GPGGA,155816.000,3844.2598,N,00908.2255,W,$GPVTG,170.23,T,,M,0.12,N,0.22,K,76063

$GPGGA,155817.000,3844.2598,N,00908.2254,W,$GPVTG,225.04,T,,M,0.07,N,0.12,K,76980

$GPGGA,155818.000,3844.2598,N,00908.2254,W,$GPVTG,39.87,T,,M,0.03,N,0.05,K,77918

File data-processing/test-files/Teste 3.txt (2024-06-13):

susp 800,0,0 
susp 1027,1028,100 
susp 1050,1010,200 
susp 1066,1019,300 
susp 1035,996,400 
susp 1009,1051,500 
susp 1025,998,600 
susp 1049,1010,700 
susp 1019,1049,800 
susp 1025,999,900 
susp 1046,1017,999 
susp 1005,1052,1099 
susp 998,1050,1199 
susp 1019,1063,1299 
susp 994,1037,1399 
susp 1031,1031,1499 
susp 1018,1062,1599 
susp 1023,1079,1699 
susp 1022,1040,1799 
susp 1031,1013,1899 
susp 1019,1068,1999 
susp 1044,1002,2099 
susp 1021,1056,2199 
susp 1057,1014,2299 
susp 1068,1027,2399 
susp 1056,1015,2499 
susp 1054,1021,2599 
susp 1010,1052,2699 
susp 1059,1016,2799 
susp 1008,1046,2899 
susp 1011,1056,2999 
susp 1004,1042,3099 
susp 1011,1058,3199 
susp 1048,1008,3299 
susp 1043,1004,3399 
susp 1012,1048,3499 
susp 1048,1003,3599 
susp 1030,1035,3699 
susp 1056,1014,3799 
susp 1027,1021,3899 
susp 989,1037,3999 
susp 1006,1054,4099 
susp 1055,1024,4199 
susp 1061,1028,4299 
susp 1035,993,4399 
susp 1015,1071,4499 
susp 1063,1031,4599 
susp 1049,1008,4699 
susp 1010,1053,4799 
susp 1054,1020,4899 
susp 1044,1003,4999 
susp 1040,1033,5099 
susp 1015,1065,5199 
susp 1065,1021,5299 
susp 1011,1056,5399 
susp 1014,1056,5499 
susp 1040,1004,5599 
susp 1030,997,5699 
susp 1013,1065,5799 
susp 1015,1060,5899 
susp 1013,1060,5999 
susp 985,1026,6099 
susp 1022,1075,6199 
susp 1049,1006,6299 
susp 1057,1017,6399 
susp 1046,1015,6499 
susp 1005,1057,6599 
susp 1063,1013,6699 
susp 1030,1062,6799 
susp 1017,1046,6899 
susp 996,1040,6999 
susp 1004,1049,7099 
susp 1049,1020,7199 
susp 1004,1026,7299 
susp 1009,1056,7399 
susp 1001,1049,7499 
susp 1007,1028,7599 
susp 1041,1078,7699 
susp 1030,1000,7799 
susp 997,1024,7899 
susp 998,1040,7999 
susp 1023,1027,8099 
susp 998,1036,8199 
susp 1031,1063,8299 
susp 993,1040,8399 
susp 1018,1053,8499 
susp 1048,1007,8599 
susp 1003,1049,8699 
susp 1060,1018,8799 
susp 1008,1056,8899 
susp 1041,1078,8999 
susp 1034,989,9099 
susp 1012,1057,9199 
susp 1049,1004,9299 
susp 1052,1017,9399 
susp 1046,1012,9499 
susp 1033,1030,9599 
susp 1028,1062,9699 
susp 1063,1019,9799 
susp 1014,1059,9899 
susp 1037,990,9999 
susp 1016,1054,10099 
susp 999,1025,10199 
susp 1046,1013,10299 
susp 1036,1071,10399 
susp 1026,1029,10499 
susp 1072,1021,10599 
susp 998,1037,10699 
susp 1007,1045,10799 
susp 1014,1041,10899 
susp 988,1033,10999 
susp 1026,1029,11099 
susp 1031,1031,11199 
susp 1018,1025,11299 
susp 1024,1054,11399 
susp 1054,1007,11499 
susp 1025,1032,11599 
susp 1042,1000,11699 
susp 1024,1061,11799 
susp 1026,1068,11899 
susp 1072,1021,11999 
susp 1064,1015,12099 
susp 1042,999,12199 
susp 1070,1021,12299 
susp 1022,1065,12399 
susp 1062,1015,12499 
susp 1048,1010,12599 
susp 1048,1018,12699 
susp 1044,1008,12799 
susp 1026,1001,12899 
susp 1049,1007,12999 
susp 1030,1029,13099 
susp 1058,1017,13199 
susp 1012,1059,13299 
susp 1019,1068,13399 
susp 1021,1059,13499 
susp 1039,1004,13599 
susp 1029,990,13699 
susp 1067,1027,13799 
susp 1016,1057,13899 
susp 995,1038,13999 
susp 1010,1053,14099 
susp 995,1040,14199 
susp 1034,990,14299 
susp 1024,1016,14399 
susp 1070,1037,14499 
susp 1041,998,14599 
susp 1066,1025,14699 
susp 1059,1018,14799 
susp 1044,1008,14899 
susp 995,1038,14999 
susp 1029,1014,15099 
susp 1011,1059,15199 
susp 1060,1021,15299 
susp 1042,999,15399 
susp 1031,1030,15499 
susp 1008,1039,15599 
susp 1028,1026,15699 
susp 1047,1010,15799 
susp 1003,1047,15899 
susp 1022,1073,15999 
susp 996,1042,16099 
susp 1010,1052,16199 
susp 1061,1027,16299 
susp 1059,1021,16399 
susp 1006,1058,16499 
susp 1006,1052,16599 
susp 1036,996,16699 
susp 994,1035,16799 
susp 1046,1031,16899 
susp 1037,1003,16998 
susp 1012,1061,17098 
susp 1069,1034,17198 
susp 1030,1036,17298 
susp 1037,1004,17398 
susp 1054,1021,17498 
susp 1052,1018,17598 
susp 991,1040,17698 
susp 1051,1010,17798 
susp 1039,1006,17898 
susp 1040,1017,17998 
susp 1051,1012,18098 
susp 1005,1044,18198 
susp 1058,1018,18298 
susp 1019,1063,18398 
susp 1050,1007,18498 
susp 1017,1060,18598 
susp 1042,998,18698 
susp 1039,1010,18798 
susp 1049,1002,18898 
susp 1011,1024,18998 
susp 996,1035,19098 
susp 1001,1025,19198 
susp 1038,1004,19298 
susp 1051,1016,19398 
susp 1065,1014,19498 
susp 1024,1067,19598 
susp 1054,1015,19698 
susp 1010,1051,19798 
susp 1032,1063,19898

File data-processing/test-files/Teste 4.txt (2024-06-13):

susp 781,0,0 
susp 1046,999,100 
susp 1047,1019,200 
susp 1020,1064,300 
susp 992,1040,400 
susp 1043,1006,500 
susp 1015,1063,600 
susp 1049,1013,700 
susp 1057,1011,800 
susp 1006,1055,900 
susp 1022,1077,999 
susp 999,1051,1099 
susp 1056,1008,1199 
susp 997,1046,1299 
susp 1019,1067,1399 
susp 1047,1010,1499 
susp 1010,1052,1599 
susp 1032,1021,1699 
susp 1021,1080,1799 
susp 1017,1041,1899 
susp 1056,1013,1999 
susp 1008,1044,2099 
susp 1066,1025,2199 
susp 1028,1024,2299 
susp 1002,1042,2399 
susp 1029,1015,2499 
susp 1011,1054,2599 
susp 1059,1021,2699 
susp 1066,1026,2799 
susp 1048,1010,2899 
susp 1046,1017,2999 
susp 1015,1058,3099 
susp 1056,1012,3199 
susp 1072,1028,3299 
susp 1021,1073,3399 
susp 1015,1062,3499 
susp 1026,1023,3599 
susp 1039,1005,3699 
susp 1034,1023,3799 
susp 1007,1058,3899 
susp 1015,1069,3999 
susp 1029,1029,4099 
susp 1009,1052,4199 
susp 1004,1043,4299 
susp 1036,998,4399 
susp 1014,1063,4499 
susp 1037,1002,4599 
susp 1025,1019,4699 
susp 1052,1013,4799 
susp 1020,1063,4899 
susp 1028,988,4999 
susp 1018,1046,5099 
susp 1074,1031,5199 
susp 1010,1054,5299 
susp 1050,1010,5399 
susp 1038,1001,5499 
susp 1040,1016,5599 
susp 1061,1025,5699 
susp 1008,1039,5799 
susp 1048,999,5899 
susp 1029,1032,5999 
susp 1024,1014,6099 
susp 1052,1008,6199 
susp 1011,1048,6299 
susp 989,1035,6399 
susp 1020,1065,6499 
susp 1065,1024,6599 
susp 1019,1054,6699 
susp 1027,1062,6799 
susp 1000,1049,6899 
susp 1050,1004,6999 
susp 1026,986,7099 
susp 1023,1027,7199 
susp 1051,1011,7299 
susp 1053,1005,7399 
susp 1037,1003,7499 
susp 1056,1006,7599 
susp 1053,1007,7699 
susp 1046,1006,7799 
susp 1061,1018,7899 
susp 1016,1045,7999 
susp 1020,1065,8099 
susp 1047,1017,8199 
susp 1058,1018,8299 
susp 1067,1014,8399 
susp 1018,1065,8499 
susp 1000,1043,8599 
susp 1024,1054,8699 
susp 1019,1054,8799 
susp 1019,1064,8899 
susp 1008,1051,8999 
susp 1013,1046,9099 
susp 1024,986,9199 
susp 1008,1048,9299 
susp 1051,1011,9399 
susp 1006,1050,9499 
susp 1031,1029,9599 
susp 1035,997,9699 
susp 1024,1066,9799 
susp 1018,1064,9899 
susp 1056,1012,9999 
susp 1061,1013,10099 
susp 1000,1039,10199 
susp 1009,1051,10299 
susp 1010,1052,10399 
susp 1003,1048,10499 
susp 1041,991,10599 
susp 1060,1012,10699 
susp 1053,1006,10799 
susp 1015,1057,10899 
susp 1061,1019,10999 
susp 1011,1044,11099 
susp 1026,1062,11199 
susp 1026,1032,11299 
susp 1008,1028,11399 
susp 1025,986,11499 
susp 1015,1025,11599 
susp 1052,1021,11699 
susp 1010,1056,11799 
susp 1003,1042,11899 
susp 1019,1060,11999 
susp 1022,1055,12099 
susp 995,1037,12199 
susp 992,1041,12299 
susp 1075,1022,12399 
susp 1052,1005,12499 
susp 1001,1026,12599 
susp 1016,1059,12699 
susp 1006,1058,12799 
susp 1014,1055,12899 
susp 1065,1021,12999 
susp 1044,1012,13099 
susp 1010,1053,13199 
susp 1028,1005,13299 
susp 1026,1024,13399 
susp 1038,1002,13499 
susp 1003,1050,13599 
susp 1047,1012,13699 
susp 1056,1017,13799 
susp 1052,1017,13899 
susp 1002,1033,13999 
susp 1014,1068,14099 
susp 1016,1057,14199 
susp 1046,1012,14299 
susp 1030,1030,14399 
susp 1030,1030,14499 
susp 1046,1011,14599 
susp 1032,985,14699 
susp 1053,1021,14799 
susp 1005,1050,14899 
susp 1045,1017,14999 
susp 1029,1031,15099 
susp 1025,1012,15199 
susp 1009,1050,15299 
susp 1056,1014,15399 
susp 1081,1036,15499 
susp 1069,1036,15599 
susp 1026,1005,15699 
susp 1048,1005,15799 
susp 1033,992,15899 
susp 1019,1066,15999 
susp 1016,1059,16099 
susp 1068,1030,16199 
susp 995,1037,16299 
susp 1018,1062,16399 
susp 1053,1012,16499 
susp 1046,1015,16599 
susp 1052,1013,16699 
susp 1052,1017,16799 
susp 1012,1056,16899 
susp 1052,1014,16998 
susp 1048,1003,17098 
susp 1004,1051,17198 
susp 1032,1021,17298 
susp 1020,1065,17398 
susp 1040,995,17498 
susp 1020,1066,17598 
susp 1058,1015,17698 
susp 1045,1015,17798 
susp 1032,1024,17898 
susp 1045,1008,17998 
susp 1054,1021,18098 
susp 1014,1067,18198 
susp 1067,1029,18298 
susp 1061,1029,18398 
susp 1062,1038,18498 
susp 1051,1015,18598 
susp 1009,1054,18698 
susp 1027,1003,18798 
susp 1035,994,18898 
susp 1006,1049,18998 
susp 977,1025,19098 
susp 1028,987,19198 
susp 1042,997,19298 
susp 1063,1020,19398 
susp 1007,1052,19498 
susp 1045,1008,19598 
susp 1068,1015,19698 
susp 1012,1047,19798 
susp 1058,1007,19898 
susp 1073,1022,19998 
susp 1037,989,20098 
susp 1028,1030,20198 
susp 1022,1066,20298 
susp 1017,1026,20398 
susp 1019,1059,20498 
susp 1007,1045,20598 
susp 1009,1056,20698 
susp 1049,1019,20798 
susp 1004,1027,20898 
susp 999,1041,20998 
susp 1075,1022,21098 
susp 1017,1060,21198 
susp 1013,1046,21298 
susp 978,1025,21398 
susp 1025,1067,21498 
susp 1052,1016,21598 
susp 1067,1021,21698 
susp 1041,1002,21798 
susp 1071,1021,21898 
susp 1003,1048,21998 
susp 1033,1080,22098 
susp 1056,1011,22198 
susp 1006,1042,22298 
susp 1056,1011,22398 
susp 1015,1024,22498 
susp 1053,1012,22598 
susp 1023,1066,22698 
susp 1005,1032,22798 
susp 1005,1037,22898 
susp 1048,1018,22998 
susp 1022,1054,23098 
susp 1072,1023,23198 
susp 1050,1005,23298 
susp 1054,1012,23398 
susp 1015,1056,23498 
susp 1050,1010,23598 
susp 1052,1007,23698 
susp 1051,1020,23798 
susp 1025,1060,23898 
susp 996,1041,23998 
susp 1003,1043,24098 
susp 1063,1021,24198 
susp 1060,1012,24298 
susp 1008,1056,24398 
susp 1032,1036,24498 
susp 1006,1028,24598 
susp 1057,1023,24698 
susp 1022,1065,24798 
susp 1003,1048,24898 
susp 1076,1022,24998 
susp 1063,1031,25098 
susp 1027,1007,25198 
susp 1057,1016,25298 
susp 1013,1063,25398 
susp 1016,1043,25498 
susp 1022,1073,25598 
susp 1059,1020,25698 
susp 1016,1060,25798 
susp 1067,1028,25898 
susp 1010,1054,25998 
susp 1038,1041,26098 
susp 1004,1051,26198 
susp 1021,1072,26298 
susp 1011,1044,26398 
susp 1047,1013,26498 
susp 1015,1060,26598 
susp 1053,1025,26698 
susp 1015,1063,26798 
susp 994,1041,26898 
susp 1053,1018,26998 
susp 1062,1027,27098 
susp 1032,1024,27198 
susp 1042,1007,27298 
susp 1014,1068,27398 
susp 993,1037,27498 
susp 1016,1056,27598 
susp 1001,1038,27698 
susp 1040,996,27798 
susp 1057,1019,27898 
susp 1020,1066,27998 
susp 1067,1028,28098 
susp 1068,1030,28198 
susp 1050,1009,28298 
susp 1008,1050,28398 
susp 1037,1005,28498 
susp 1048,1003,28598 
susp 1008,1056,28698 
susp 1014,1059,28798 
susp 1026,1000,28898 
susp 1010,1052,28998 
susp 1034,1007,29098 
susp 1012,1051,29198 
susp 1043,1003,29298 
susp 999,1054,29398 
susp 1048,1004,29498 
susp 1022,1081,29598 
susp 1046,1005,29698 
susp 1042,1007,29798 
susp 1020,1052,29898 
susp 1039,1011,29998 
susp 992,1034,30098 
susp 1020,1065,30198 
susp 1025,1017,30298 
susp 1001,1041,30398 
susp 1016,1049,30498 
susp 1048,1004,30598 
susp 1034,1023,30698 
susp 1017,1060,30798 
susp 1014,1065,30898 
susp 1007,1061,30998 
susp 1026,1018,31098 
susp 1016,1059,31198 
susp 1018,1052,31298 
susp 1009,1027,31398 
susp 1006,1045,31498 
susp 1022,1028,31598 
susp 1064,1018,31698 
susp 1009,1029,31798 
susp 1025,1061,31898 
susp 1040,1008,31998 
susp 1063,1020,32098 
susp 1004,1042,32198 
susp 1021,1059,32298 
susp 1046,1013,32398 
susp 1006,1050,32498 
susp 1054,1011,32598 
susp 999,1042,32698 
susp 1022,1033,32798 
susp 1028,1028,32898 
susp 1051,1015,32998 
susp 1015,1041,33097 
susp 1014,1058,33197 
susp 1037,1038,33297 
susp 1005,1032,33397 
susp 1058,1016,33497 
susp 1032,1001,33597 
susp 1030,1063,33697 
susp 1072,1023,33797 
susp 1050,1016,33897 
susp 1012,1058,33997 
susp 1055,1018,34097 
susp 1040,1008,34197 
susp 1020,1055,34297 
susp 1021,1026,34397 
susp 1016,1025,34497 
susp 1061,1023,34597 
susp 1040,1010,34697 
susp 1048,998,34797 
susp 1028,1068,34897 
susp 1038,1004,34997 
susp 988,1033,35097 
susp 1022,1033,35197 
susp 1013,1054,35297 
susp 1034,1071,35397 
susp 1052,1010,35497 
susp 1027,1028,35597 
susp 1045,1002,35697 
susp 1015,1031,35797 
susp 1057,1016,35897 
susp 1066,1014,35997 
susp 1008,1028,36097 
susp 996,1031,36197 
susp 1009,1052,36297 
susp 1067,1020,36397 
susp 1026,1072,36497 
susp 1016,1053,36597 
susp 1040,990,36697 
susp 1050,1010,36797 
susp 1017,1058,36897 
susp 1062,1013,36997 
susp 1078,1023,37097 
susp 1060,1018,37197 
susp 1064,1013,37297 
susp 1006,1048,37397 
susp 1010,1051,37497 
susp 1038,1002,37597 
susp 998,1049,37697 
susp 1007,1060,37797 
susp 1046,1015,37897 
susp 1058,1018,37997 
susp 1015,1064,38097 
susp 1024,1016,38197 
susp 1024,1013,38297 
susp 1067,1026,38397 
susp 1002,1035,38497 
susp 990,1042,38597 
susp 1059,1018,38697 
susp 1045,1010,38797 
susp 1022,1079,38897 
susp 1014,1069,38997 
susp 1046,1012,39097 
susp 993,1036,39197 
susp 1009,1050,39297 
susp 1017,1065,39397 
susp 1051,1007,39497 
susp 1045,1019,39597 
susp 1040,999,39697 
susp 1000,1039,39797 
susp 1055,1027,39897 
55,0,0,0,0,0,0,0,0,2012
52,0,0,0,0,0,0,0,0,2022
54,0,0,0,0,0,0,0,0,2032
53,0,0,0,0,0,0,0,0,2042
51,0,0,0,0,0,0,0,0,2053
50,0,0,0,0,0,0,0,0,2055
123,0,0,0,0,0,0,0,0,2318
55,0,0,0,0,0,0,0,0,4348
52,0,0,0,0,0,0,0,0,4359
54,0,0,0,0,0,0,0,0,4369
53,0,0,0,0,0,0,0,0,4379
51,0,0,0,0,0,0,0,0,4389
50,0,0,0,0,0,0,0,44,4391
123,0,0,0,0,0,0,0,0,4654
55,0,0,0,0,0,0,0,0,6683
52,0,0,0,0,0,0,0,0,6693
54,0,0,0,0,0,0,0,0,6703
53,0,0,0,0,0,0,0,0,6713
51,0,0,0,0,0,0,0,0,6723
50,0,0,0,0,0,0,0,44,6726
123,0,0,0,0,0,0,0,0,6989
55,0,0,0,0,0,0,0,0,9017
52,0,0,0,0,0,0,0,0,9027
54,0,0,0,0,0,0,0,0,9037
53,0,0,0,0,0,0,0,0,9048
51,0,0,0,0,0,0,0,0,9058
50,0,0,0,0,0,0,0,44,9060
123,0,0,0,0,0,0,0,0,9323
55,0,0,0,0,0,0,0,0,11352
52,0,0,0,0,0,0,0,0,11362
54,0,0,0,0,0,0,0,0,11372
53,0,0,0,0,0,0,0,0,11382
51,0,0,0,0,0,0,0,0,11392
50,0,0,0,0,0,0,0,44,11395
123,0,0,0,0,0,0,0,0,11657
55,0,0,0,0,0,0,0,0,13685
52,0,0,0,0,0,0,0,0,13695
54,0,0,0,0,0,0,0,0,13705
53,0,0,0,0,0,0,0,0,13716
51,0,0,0,0,0,0,0,0,13726
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
$GPGGA,235942.800,,,,,$GPVTG,0.00,T,,M,0.00,N,0.00,K,2763

$GPGGA,235943.800,,,,,$GPVTG,0.00,T,,M,0.00,N,0.00,K,3845

$GPGGA,235945.799,,,,,$GPVTG,0.00,T,,M,0.00,N,0.00,K,4943

$GPGGA,235946.799,,,,,$GPVTG,0.00,T,,M,0.00,N,0.00,K,6806

$GPGGA,235949.799,,,,,$GPVTG,0.00,T,,M,0.00,N,0.00,K,9760

$GPGGA,235950.800,,,,,$GPVTG,0.00,T,,M,0.00,N,0.00,K,10842

$GPGGA,235953.452,,,,,$GPVTG,0.00,T,,M,0.00,N,0.00,K,12654

$GPGGA,173208.089,,,,,$GPVTG,0.00,T,,M,0.00,N,0.00,K,14495

$GPGGA,173211.089,,,,,$GPVTG,0.00,T,,M,0.00,N,0.00,K,16632

$GPGGA,173212.089,,,,,$GPVTG,0.00,T,,M,0.00,N,0.00,K,17717

$GPGGA,173213.089,,,,,$GPVTG,0.00,T,,M,0.00,N,0.00,K,19482

$GPGGA,173217.089,,,,,$GPVTG,0.00,T,,M,0.00,N,0.00,K,22620

$GPGGA,173218.089,,,,,$GPVTG,0.00,T,,M,0.00,N,0.00,K,23668

$GPGGA,173218.298,,,,,$GPVTG,0.00,T,,M,0.00,N,0.00,K,23985

$GPGGA,173219.298,,,,,$GPVTG,0.00,T,,M,0.00,N,0.00,K,25692

$GPGGA,173220.298,,,,,$GPVTG,0.00,T,,M,0.00,N,0.00,K,26733

$GPGGA,173221.298,,,,,$GPVTG,0.00,T,,M,0.00,N,0.00,K,27778

$GPGGA,173224.099,,,,,$GPVTG,0.00,T,,M,0.00,N,0.00,K,29697

$GPGGA,173225.099,,,,,$GPVTG,0.00,T,,M,0.00,N,0.00,K,30720

$GPGGA,173226.099,,,,,$GPVTG,0.00,T,,M,0.00,N,0.00,K,31761

$GPGGA,173227.099,,,,,$GPVTG,0.00,T,,M,0.00,N,0.00,K,33552

$GPGGA,173228.099,,,,,$GPVTG,0.00,T,,M,0.00,N,0.00,K,34588

$GPGGA,173231.094,,,,,$GPVTG,98.02,T,,M,0.05,N,0.09,K,36614

$GPGGA,173232.094,,,,,$GPVTG,356.58,T,,M,0.30,N,0.55,K,37637

$GPGGA,173234.000,3844.2495,N,00908.2268,W,$GPVTG,17.71,T,,M,0.09,N,0.17,K,39556

$GPGGA,173236.000,3844.2501,N,00908.2266,W,$GPVTG,149.71,T,,M,0.27,N,0.50,K,41716

$GPGGA,173237.000,3844.2498,N,00908.2268,W,$GPVTG,178.03,T,,M,0.32,N,0.59,K,42645

$GPGGA,173239.000,3844.2497,N,00908.2269,W,$GPVTG,181.74,T,,M,0.48,N,0.88,K,44780

$GPGGA,173240.000,3844.2494,N,00908.2270,W,$GPVTG,172.18,T,,M,0.54,N,1.00,K,45703

$GPGGA,173241.000,3844.2497,N,00908.2270,W,$GPVTG,168.50,T,,M,0.55,N,1.02,K,46617
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

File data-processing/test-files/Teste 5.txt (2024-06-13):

55,185,185,187,184,185,185,0,0,2652
52,186,185,185,183,186,187,0,0,2664
54,186,187,182,181,186,184,0,0,2676
53,186,190,186,185,188,187,0,0,2687
51,0,181,194,188,0,0,0,0,2699
50,122,231,232,230,231,1,0,0,2701
123,25,24,25,0,7,255,255,255,3087
55,185,185,187,184,185,185,0,0,5776
52,186,185,185,183,186,187,0,0,5787
54,186,187,182,181,186,184,0,0,5799
53,186,190,186,185,188,187,0,0,5810
51,0,181,194,188,0,0,0,0,5821
50,120,231,232,230,231,1,25,43,5824
123,25,24,25,0,15,255,255,255,6209
55,185,185,187,184,185,185,0,0,8895
52,186,185,185,183,186,187,0,0,8906
54,186,187,182,181,186,184,0,0,8918
53,186,190,186,185,188,187,0,0,8929
51,0,181,194,188,0,0,0,0,8940
50,120,231,232,230,231,1,25,43,8943
123,25,24,25,0,15,255,255,255,9329
128,6169,25,65295,65535,9768
11,0,0,2,23,9768
12,0,0,0,0,9768
13,0,649,2,1789,9769
14,1261,27,0,0,9769
15,0,0,136,0,9769
128,0,649,2,1789,9969
11,0,0,0,65503,9969
12,0,0,0,0,9969
13,0,649,7,1789,9969
14,1261,27,0,0,9970
15,0,0,127,0,9970
128,1261,27,0,0,10170
11,0,0,4,14,10170
12,0,0,0,0,10170
13,0,649,12,1786,10170
14,1697,27,0,0,10171
15,0,0,134,0,10171
128,0,649,12,1786,10371
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
susp 797,0,0 
susp 1064,1020,100 
susp 1056,1016,200 
susp 1017,1046,300 
susp 1021,1018,400 
susp 1008,1048,500 
susp 1002,1046,600 
susp 1039,1008,700 
susp 1039,1006,800 
susp 1016,1054,900 
susp 1042,1007,999 
susp 1008,1050,1099 
susp 1061,1025,1199 
susp 1063,1032,1299 
susp 995,1038,1399 
susp 1022,1076,1499 
susp 1021,1058,1599 
susp 991,1041,1699 
susp 990,1036,1799 
susp 1064,1017,1899 
susp 1018,1065,1999 
susp 1069,1034,2099 
susp 1050,1007,2199 
susp 1036,1015,2299 
susp 1033,991,2399 
susp 1005,1056,2499 
susp 1028,1026,2599 
susp 1003,1049,2699 
susp 1015,1075,2799 
susp 1039,1009,2899 
susp 1064,1019,2999 
susp 1036,996,3099 
susp 1006,1059,3199 
susp 1031,1034,3299 
susp 1030,999,3399 
susp 1020,1069,3499 
susp 1047,1014,3599 
susp 1065,1023,3699 
susp 1038,1005,3799 
susp 1028,993,3899 
susp 1055,1023,3999 
susp 1031,1036,4099 
susp 1002,1042,4199 
susp 1014,1063,4299 
susp 1030,1030,4399 
susp 1015,1070,4499 
susp 1011,1054,4599 
susp 1031,1014,4699 
susp 1025,994,4799 
susp 1024,981,4899 
susp 1047,1019,4999 
susp 1057,1014,5099 
susp 1066,1023,5199 
susp 998,1049,5299 
susp 1044,1001,5399 
susp 1073,1030,5499 
susp 1018,1056,5599 
susp 1003,1043,5699 
susp 1022,1080,5799 
susp 1050,1013,5899 
susp 998,1048,5999 
susp 1017,1059,6099 
susp 1023,1061,6199 
susp 1010,1052,6299 
susp 1009,1053,6399 
susp 1038,1010,6499 
susp 1058,1016,6599 
susp 1002,1033,6699 
susp 1014,1040,6799 
susp 1012,1025,6899 
susp 1014,1053,6999 
susp 1041,999,7099 
susp 1028,1030,7199 
susp 1067,1015,7299 
susp 1038,991,7399 
susp 1003,1039,7499 
susp 991,1040,7599 
susp 1002,1048,7699 
susp 1065,1015,7799 
susp 1008,1045,7899 
susp 1061,1014,7999 
susp 1057,1016,8099 
susp 1032,1075,8199 
susp 1025,1072,8299 
susp 1016,1042,8399 
susp 1010,1024,8499 
susp 1033,1031,8599 
susp 1049,1020,8699 
susp 1038,997,8799 
susp 1000,1041,8899 
susp 991,1034,8999 
susp 1056,1015,9099 
susp 1050,1010,9199 
susp 1066,1014,9299 
susp 1068,1020,9399 
susp 1004,1044,9499 
susp 1027,1068,9599 
susp 1026,1072,9699 
susp 1062,1023,9799 
susp 1027,994,9899 
susp 1041,1002,9999 
susp 1042,1010,10099 
susp 1011,1050,10199 
susp 1052,1011,10299 
susp 1065,1020,10399 
susp 1061,1015,10499 
susp 1005,1039,10599 
susp 1017,1026,10699 
susp 1013,1056,10799 
susp 1046,1009,10899 
susp 1002,1038,10999 
susp 1055,1022,11099 
susp 1019,1065,11199 
susp 1011,1052,11299 
susp 1078,1023,11399 
susp 1067,1021,11499 
susp 1019,1054,11599 
susp 1045,1006,11699 
susp 1058,1016,11799 
susp 1045,1011,11899 
susp 1066,1020,11999 
susp 1020,1026,12099 
susp 1047,1009,12199 
susp 1012,1051,12299 
susp 1005,1044,12399 
susp 1018,1065,12499 
susp 1017,1064,12599 
susp 1050,1009,12699 
susp 1016,1057,12799 
susp 983,1036,12899 
susp 1020,1069,12999 
susp 1023,1077,13099 
susp 1038,1006,13199 
susp 1028,986,13299 
susp 1043,1000,13399 
susp 1014,1052,13499 
susp 1066,1024,13599 
susp 1060,1024,13699 
susp 1016,1039,13799 
susp 1030,996,13899 
susp 1034,991,13999 
susp 1045,1009,14099 
susp 1025,1000,14199 
susp 1005,1055,14299 
susp 997,1045,14399 
susp 1026,1002,14499 
susp 1068,1030,14599 
susp 1012,1058,14699 
susp 1006,1062,14799 
susp 1009,1057,14899 
susp 1054,1025,14999 
susp 1056,1017,15099 
susp 999,1052,15199 
susp 1004,1043,15299 
susp 1036,999,15399 
susp 1014,1068,15499 
susp 1018,1047,15599 
susp 1017,1062,15699 
susp 1057,1011,15799 
susp 1057,1019,15899 
susp 1043,1010,15999 
susp 1006,1057,16099 
susp 1040,1004,16199 
susp 1043,1003,16299 
susp 1026,1002,16399 
susp 1021,1057,16499 
susp 1006,1053,16599 
susp 1014,1055,16699 
susp 984,1027,16799 
susp 1019,1067,16899 
susp 996,1045,16998 
susp 1040,1003,17098 
susp 1026,982,17198 
susp 1024,997,17298 
susp 1020,1069,17398 
susp 1040,1003,17498 
susp 1055,1020,17598 
susp 1048,1005,17698 
susp 1062,1024,17798 
susp 1017,1056,17898 
susp 1017,1059,17998 
susp 1010,1053,18098 
susp 1012,1048,18198 
susp 1044,1005,18298 
susp 1000,1040,18398 
susp 1045,1007,18498 
susp 1005,1055,18598 
susp 1018,1060,18698 
susp 1026,1013,18798 
susp 1021,1076,18898 
susp 1027,1062,18998 
susp 1012,1052,19098 
susp 1034,989,19198 
susp 1065,1015,19298 
susp 1064,1015,19398 
susp 1047,1013,19498 
susp 1027,1034,19598 
susp 1066,1022,19698 
susp 1022,1062,19798 
susp 1034,1076,19898 
14,1794,27,0,0,18730
15,0,0,142,0,18730
123,25,24,25,0,7,255,255,255,18730
128,1794,27,0,0,18816
11,0,0,1,65511,18816
12,0,0,0,0,18816
13,0,649,37,1788,18817
14,1793,27,0,0,18817
15,0,0,137,0,18817
128,0,649,37,1788,19017
11,0,0,1,11,19017
12,0,0,0,0,19017
13,0,649,37,1787,19018
14,1792,27,0,0,19018
15,0,0,130,0,19018
128,1792,27,0,0,19218
11,0,0,8,17,19218
12,0,0,0,0,19218
13,0,649,37,1788,19219
14,1793,27,0,0,19219
15,0,0,139,0,19219
128,0,649,37,1788,19419
11,0,0,3,65531,19419
12,0,0,0,0,19419
13,0,649,37,1789,19420
14,1793,27,0,0,19420
15,0,0,133,0,19420
128,0,649,37,1789,19620
11,0,0,2,65531,19620
12,0,0,0,0,19621
13,0,649,37,1789,19621
14,1793,27,0,0,19621
15,0,0,134,0,19621
128,0,649,37,1789,19821
11,0,0,65528,6,19821
12,0,0,0,0,19822
13,0,649,37,1789,19822
14,1794,27,0,0,19822
15,0,0,133,0,19822
128,0,649,37,1789,20503
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
susp 1056,1016,19998 
susp 1025,1045,20098 
susp 1005,1039,20198 
susp 1067,1015,20298 
susp 1022,1066,20398 
susp 995,1041,20498 
susp 1024,1028,20598 
susp 1056,1006,20698 
susp 1038,991,20798 
susp 1018,1059,20898 
susp 1014,1051,20998 
susp 1027,1072,21098 
susp 1017,1024,21198 
susp 1053,1005,21298 
susp 1052,1005,21398 
susp 1053,1007,21498 
susp 1027,1072,21598 
susp 1054,1016,21698 
susp 1018,1054,21798
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

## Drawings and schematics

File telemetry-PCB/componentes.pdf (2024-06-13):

# State 1 2

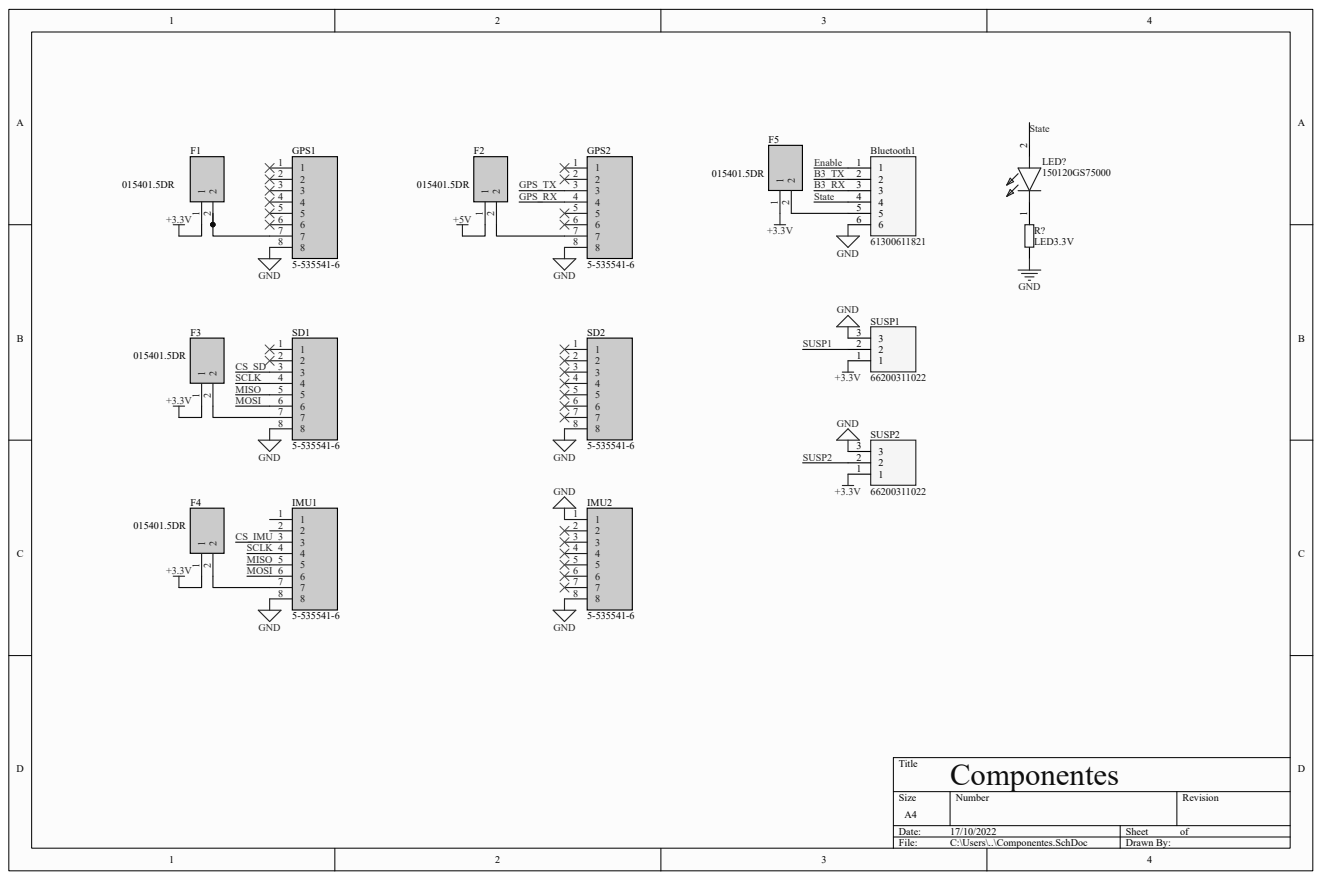
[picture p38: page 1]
Title; Size; Number; Revision; Date:; Sheet; File:; C:\Users\..\Componentes.SchDoc; Drawn By:; GPS1; GPS2; IMU1; IMU2; GND; GPS_TX GPS_RX; MOSI; SCLK; MISO; CS_IMU SCLK MISO MOSI; Componentes; Bluetooth1; GND ¹; SUSP1; SUSP2; Enable; State; LED? 150120GS75000; R? LED3.3V

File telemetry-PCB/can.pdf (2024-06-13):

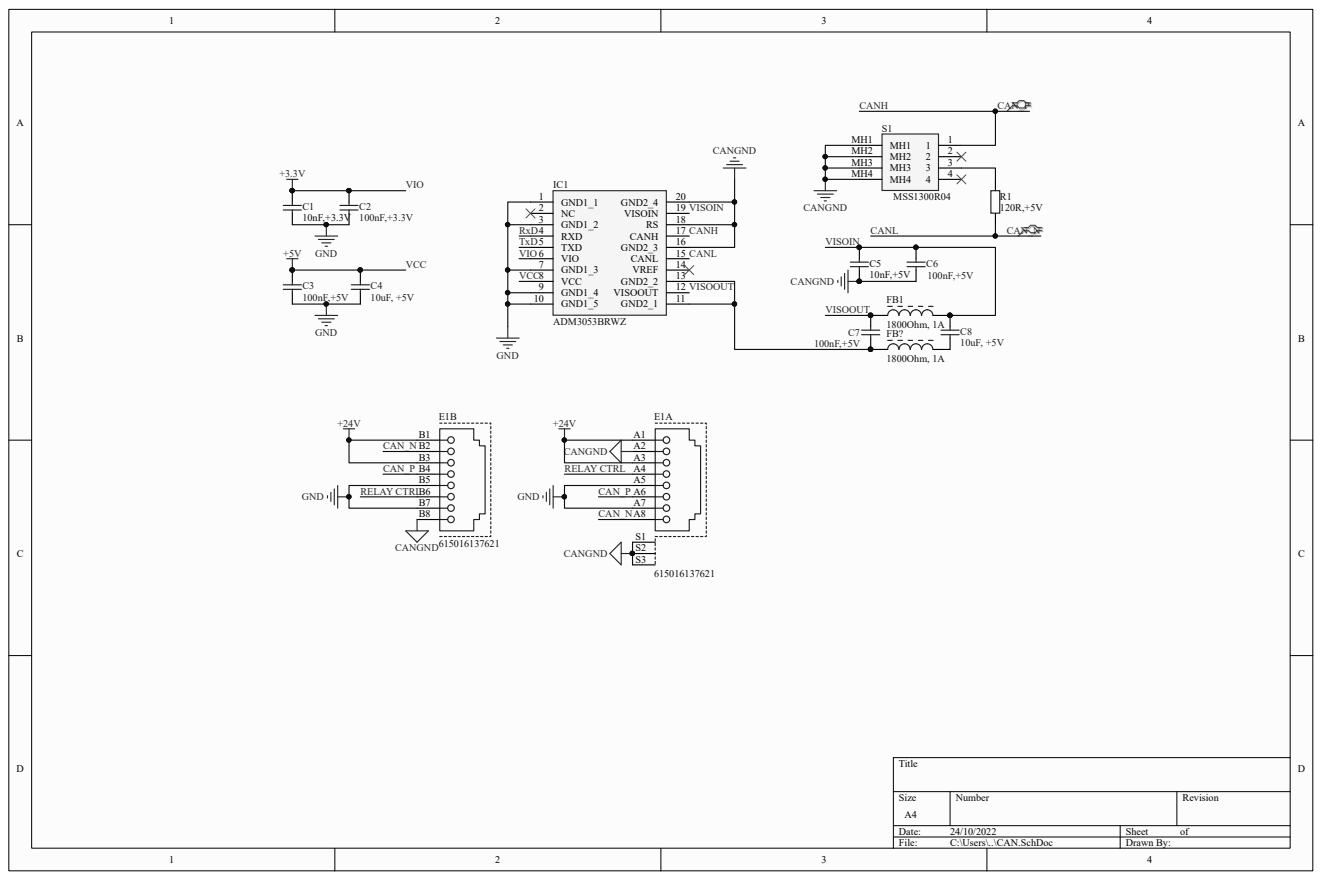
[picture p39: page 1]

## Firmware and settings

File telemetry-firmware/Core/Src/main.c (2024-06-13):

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
/* Includes ------------------------------------------------------------------*/
#include "main.h"
#include "fatfs.h"

/* USER CODE BEGIN Includes */
#include "stdio.h"
#include "stdlib.h"
#include "string.h"
#include "ICM20948.h"
#include "fatfs_sd.h"
/* USER CODE END Includes */

/* USER CODE BEGIN PD */
#define V_ADC 3.3/4096

#define GPS_Enable 1;
#define GPS_Disables 0;
#define ICM_Enable 1;
#define ICM_Disable 0;
#define POT_Enable 1;
#define POT_Disable 0;
#define Servo_Enable 1;
#define Servo_Disable 0;

//#define DRCPATTISON 1
//#define CORYCLINE 2

/* USER CODE END PD */

ADC_HandleTypeDef hadc1;
DMA_HandleTypeDef hdma_adc1;

CAN_HandleTypeDef hcan1;
CAN_HandleTypeDef hcan2;

SPI_HandleTypeDef hspi1;
DMA_HandleTypeDef hdma_spi1_rx;
DMA_HandleTypeDef hdma_spi1_tx;

TIM_HandleTypeDef htim2;

UART_HandleTypeDef huart4;
UART_HandleTypeDef huart2;
DMA_HandleTypeDef hdma_uart4_rx;

/* USER CODE BEGIN PV */
int  GPS_ready = 0;
int start_race = 0;
uint32_t GPS_BR=9600;
int time_count=0;
int time_total=0;
// SD CARD RELATED ///////////////////////////////////////////////////////////////////////////////////////////
FATFS fs;  // file system
FIL fil; // File
FILINFO fno;
FRESULT fresult;  // result
UINT br, bw;  // File read/write count

/**** capacity related *****/
FATFS *pfs;
DWORD fre_clust;
uint32_t total, free_space;

#define BUFFER_SIZE 128
char buffer[BUFFER_SIZE];  // to store strings..
//////////////////////////////////////////////////////////////////////////////////////////////////////////////

// CAN ///////////////////////////////////////////////////////////////////////////////////////////////////////
CAN_TxHeaderTypeDef pTxHeader;
uint32_t pTxMailbox;

CAN_RxHeaderTypeDef pRxHeader;
uint32_t pRxMailbox;

CAN_FilterTypeDef CAN_filter1;
//////////////////////////////////////////////////////////////////////////////////////////////////////////////

//CAN UNION

union CAN_M{
	int i[2];
	float f[2];
	uint8_t bytes[8];
} can_m;

union CAN_M tx_union;
union CAN_M rx_union;
uint8_t can_m_received=0;

#define Especial	50  // Total Voltage :: V1t :: P2t :: P3t :: P4t :: P5t :: Max Temp :: Pack Ref ::
#define PACK_V_1	51  // All 6 voltages
#define PACK_V_2	52  // All 6 voltages
#define PACK_V_3	53  // All 6 voltages
#define PACK_V_4	54  // All 6 voltages
#define PACK_V_5	55  // All 6 voltages
#define PACK_1_2	121 // All 4 temperatures
#define PACK_3_4	122 // All 4 temperatures
#define PACK_5		123 // All 4 temperatures
#define Tele_SR		90
/* USER CODE END PV */

void SystemClock_Config(void);
static void MX_GPIO_Init(void);
static void MX_DMA_Init(void);
static void MX_CAN1_Init(void);
static void MX_CAN2_Init(void);
static void MX_SPI1_Init(void);
static void MX_ADC1_Init(void);
static void MX_TIM2_Init(void);
static void MX_UART4_Init(void);
static void MX_USART2_UART_Init(void);
/**
  * @brief  The application entry point.
  * @retval int
  */

int _write(int32_t file, uint8_t *ptr, int32_t len)
{
    for (int i = 0; i < len; i++)
    {
        ITM_SendChar(*ptr++);
    }
    return len;
}

int main(void)
{
  /* USER CODE BEGIN 1 */
	char *token, *string;
	uint8_t buff[1200];
	char buffStr[600];
	char nmeaSnt[80];
	uint8_t intSum;
	char hex[2];
	int i,j, file=0;

	////////////////////////////////////////////////////////////////////////////////////

	char *rawSum;
	char smNmbr[3];

	uint8_t cnt = 0;

	//////////////////////////////////////////////////////////////////////////////////////////////////
	/*char daytime[6];
	char valid;
	char lat[9];
	char hemLat;
	char lon[10];
	char hemLon;
	char speed[4];
	char track[6];
	char date[6];
	char variation[5];
	char orientation;

	char *daytime_raw;
	char *valid_raw;
	char *lat_raw;
	char *hemLat_raw;
	char *lon_raw;
	char *hemLon_raw;
	char *speed_raw;
	char *track_raw;
	char *date_raw;
	char *variation_raw;
	char *orientation_raw;*/
//////////////////////////////////////////////////// EXTRA ME

	uint8_t valid_5,valid_4,valid_3,valid_2,valid_1,valid_t;
	uint8_t pack[6][6], tempack[5][4], templacas[3];
	/////////////////////////////////////////


  /* USER CODE END 1 */

  /* MCU Configuration--------------------------------------------------------*/

  /* Reset of all peripherals, Initializes the Flash interface and the Systick. */
  HAL_Init();

  /* Configure the system clock */
  SystemClock_Config();

  /* Initialize all configured peripherals */
  MX_GPIO_Init();
  MX_DMA_Init();
  MX_CAN1_Init();
  MX_CAN2_Init();
  MX_SPI1_Init();
  MX_ADC1_Init();
  MX_TIM2_Init();
  MX_UART4_Init();
  MX_USART2_UART_Init();
  MX_FATFS_Init();
  /* USER CODE BEGIN 2 */

	uint32_t value[2];
	uint32_t suspension1,suspension2;
	HAL_StatusTypeDef manager;


	// Inicializar UART4 e o ADC /////////////
	//HAL_UART_Receive_DMA(&huart4, buff, 1200);
	//HAL_Delay(100); //necessario?
	//HAL_ADC_Start_DMA(&hadc1, value, 2); //sem pot's
	//////////////////////////////////////////

  /* USER CODE END 2 */

  /* Infinite loop */
  /* USER CODE BEGIN WHILE */

  	// CAN Initiations ///////////////////////////////////////////////////////////////////////////////////////
  	HAL_CAN_Start(&hcan2);
  	HAL_CAN_ActivateNotification(&hcan2, CAN_IT_RX_FIFO0_MSG_PENDING);
  	//HAL_CAN_DeactivateNotification(&hcan2, CAN_IT_RX_FIFO0_MSG_PENDING);
	CAN_filter1.FilterBank = 14;
	CAN_filter1.FilterMode = CAN_FILTERMODE_IDMASK;
	CAN_filter1.FilterScale = CAN_FILTERSCALE_32BIT;
	CAN_filter1.FilterIdHigh = 0x0000;
	CAN_filter1.FilterIdLow = 0x0000; //00FF
	CAN_filter1.FilterMaskIdHigh = 0x0000; //FFFF
	CAN_filter1.FilterMaskIdLow = 0x0000; //FF00
	CAN_filter1.FilterFIFOAssignment = CAN_RX_FIFO0;
	CAN_filter1.FilterActivation = ENABLE;
	CAN_filter1.SlaveStartFilterBank = 14;

	HAL_CAN_ConfigFilter(&hcan2, &CAN_filter1);

	// USED FOR PUTTING BAUDRATE AT 115200 /////
	/*uint8_t *set = "$PMTK251,115200*1F\r\n";
	manager=HAL_UART_Transmit(&huart4, set, 21, 1000);
	if(manager != HAL_OK)
	{
		printf("Error 1: Changing GPS baudrate.\r\n");
		while(1){

		}
	}*/
	//GPS_BR=115200;
	//HAL_UART_DeInit(&huart4);
	//////////////MX_UART4_Init();
	//HAL_UART_Init(&huart4);
	//HAL_UART_Receive_DMA(&huart4, buff, 1200);
	////////////////////////////////////////////

	// ICM INITIALIZATIONS ///////////////////////////////////////////////////////////////////////////////////
#if defined(ICM_Enable)
	HAL_GPIO_WritePin(GPIOC, GPIO_PIN_5, SET); // SDCard
	HAL_GPIO_WritePin(GPIOB, GPIO_PIN_0, SET); // IMU
	ICM_PowerOn();
	HAL_Delay(10); // Ainda falta ver se estes valores do ICM são normais antes de estar a ler.
#endif
	//////////////////////////////////////////////////////////////////////////////////////////////////////////

	//SD CARD INIT ///////////////////////////////////////////////////////////////////////////////////////////
	fresult = f_mount(&fs, "/", 1);
	if (fresult != FR_OK)
	{

		printf("Error 2: Mounting SDCARD.\r\n");
		while(1)
		{

		}
	}

	f_getfree("", &fre_clust, &pfs);
	total = (uint32_t)((pfs->n_fatent - 2) * pfs->csize * 0.5);
	printf("SD CARD Total Size: \t%lu\n",total);
	free_space = (uint32_t)(fre_clust * pfs->csize * 0.5);
	printf("SD CARD Free Space: \t%lu\n\n",free_space);

	if(free_space < total/8)
	{
		printf("Error 3: 1/8 left. \r\n");
		while(1){

		}
	}

	/*while(1){

	}*/
	//////////////////////////////////////////////////////////////////////////////////////////////////////////
	int var=0;
	while(1)
	{
		pTxHeader.DLC=1;
		pTxHeader.IDE=CAN_ID_STD;
		pTxHeader.RTR=CAN_RTR_DATA;
		pTxHeader.StdId=Especial;
		tx_union.bytes[0]=224;
		tx_union.bytes[1]=250;
		tx_union.bytes[2]=260;
		tx_union.bytes[3]=180;
		tx_union.bytes[4]=165;
		tx_union.bytes[5]=165;
		HAL_CAN_AddTxMessage(&hcan2, &pTxHeader, &tx_union, &pTxMailbox);
		while(1)
		{
			for (var=0; var < 1000; var++ )
			{

			}
			break;
		}

	}
    /* USER CODE END WHILE */

    /* USER CODE BEGIN 3 */
	while(1)
	{
		can_m_received=1;
		if(can_m_received==1)
		{
			if(pRxHeader.StdId==Tele_SR)
			{
				if(rx_union.bytes[0]==0)
				{
					start_race=1;
					tx_union.bytes[0]=1;
				}
				else if(rx_union.bytes[0]==1)
				{
					start_race=0;
					tx_union.bytes[0]=0;
				}
					pTxHeader.DLC=1;
					pTxHeader.IDE=CAN_ID_STD;
					pTxHeader.RTR=CAN_RTR_DATA;
					pTxHeader.StdId=Tele_SR;
					HAL_CAN_AddTxMessage(&hcan2, &pTxHeader, &tx_union, &pTxMailbox);
			}

			//tensões para os packs de bateria
			for(i=50;i<56;i++)
			{
				if(pRxHeader.StdId==i && start_race==1){
					pack[i-50][0]=rx_union.bytes[0];
					pack[i-50][1]=rx_union.bytes[1];
					pack[i-50][2]=rx_union.bytes[2];
					pack[i-50][3]=rx_union.bytes[3];
					pack[i-50][4]=rx_union.bytes[4];
					pack[i-50][5]=rx_union.bytes[5];
					//printf("p1 %d  p2 %d  p3 %d  p4 %d  p5 %d pt %d\n\r",pack[i-50][0],pack[i-50][1],pack[i-50][2],pack[i-50][3],pack[i-50][4],pack[i-50][5]);
				}
			}
			pRxHeader.StdId=121;
			start_race=1;
			//temperatura para o primeiro e segundo pack de baterias
			if(pRxHeader.StdId==121 && start_race==1){
				tempack[0][0]/rx_union.bytes[0];
				tempack[0][1]=rx_union.bytes[1];
				tempack[0][2]=rx_union.bytes[2];
				tempack[0][3]=rx_union.bytes[3];
				tempack[1][0]=rx_union.bytes[4];
				tempack[1][1]=rx_union.bytes[5];
				tempack[1][2]=rx_union.bytes[6];
				tempack[1][3]=rx_union.bytes[7];
				//printf("p1c1 %d  p1c2 %d  p1c3 %d  p1c4 %d  p2c1 %d p2c2 %d p2c3 %d p2c4 %d \n\r",tempack[0][0],tempack[0][1],tempack[0][2],tempack[0][3],tempack[1][0],tempack[1][1],tempack[1][2], tempack[1][3]);
			}
			//temperatura para o terceiro e quarto pack de baterias
			if(pRxHeader.StdId==121 && start_race==1){
				tempack[2][0]=rx_union.bytes[0];
				tempack[2][1]=rx_union.bytes[1];
				tempack[2][2]=rx_union.bytes[2];
				tempack[2][3]=rx_union.bytes[3];
				tempack[3][0]=rx_union.bytes[4];
				tempack[3][1]=rx_union.bytes[5];
				tempack[3][2]=rx_union.bytes[6];
				tempack[3][3]=rx_union.bytes[7];
				//printf("p1 %d  p2 %d  p3 %d  p4 %d  p5 %d pt %d\n\r",pack[i-50][0],pack[i-50][1],pack[i-50][2],pack[i-50][3],pack[i-50][4],pack[i-50][5]);
			}
			//temperatura para o quinto pack de baterias
			if(pRxHeader.StdId==121 && start_race==1){
				tempack[4][0]=rx_union.bytes[0];
				tempack[4][1]=rx_union.bytes[1];
				tempack[4][2]=rx_union.bytes[2];
				tempack[4][3]=rx_union.bytes[3];
				//printf("p1 %d  p2 %d  p3 %d  p4 %d  p5 %d pt %d\n\r",pack[i-50][0],pack[i-50][1],pack[i-50][2],pack[i-50][3],pack[i-50][4],pack[i-50][5]);
			}
			//temperatura para as placas
			for(i=131;i<134;i++)
			{
				if(pRxHeader.StdId==i && start_race==1)
				{
					templacas[i-131]=rx_union.bytes[0];
				}
			}

			can_m_received=0;
		}

		HAL_CAN_ActivateNotification(&hcan2, CAN_IT_RX_FIFO0_MSG_PENDING);

			if(can_m_received==1)
			{
				if(pRxHeader.StdId==Tele_SR)
				{
					if(rx_union.bytes[0]==0)
					{
						start_race=1;
						tx_union.bytes[0]=1;
					}
					else if(rx_union.bytes[0]==1)
					{
						start_race=0;
						tx_union.bytes[0]=0;
					}
					can_m_received=0;
					pTxHeader.DLC=1;
					pTxHeader.IDE=CAN_ID_STD;
					pTxHeader.RTR=CAN_RTR_DATA;
					pTxHeader.StdId=Tele_SR;

				HAL_CAN_AddTxMessage(&hcan2, &pTxHeader, &tx_union, &pTxMailbox);
				}
			}

		if(start_race==1)
		{
			valid_t=1;
			if(time_count>=10 && valid_t==1)
			{

				//GPS READINGS ///////////////////////////////////////////////////////////////////////////
#if defined(GPS_Enable)
				while(GPS_ready!=1)
				{
					GPS_ready=1;
				}

				memset(buffStr, 0, 600);

				sprintf(buffStr, "%s", buff);

				string = strdup(buffStr);

				while ((token = strsep(&string, "\n")) != NULL)
				{

					memset(nmeaSnt, 0, 80);

					sprintf(nmeaSnt, "%s", token);

					printf("%s", nmeaSnt);

					// selecting only $GNGLL sentences, combined GPS and GLONASS
					// on my GPS sensor this good NMEA sentence is always 50 characters
					if ( strstr(nmeaSnt, "$GPRMC") != 0 && strlen(nmeaSnt) > 49 && strstr(nmeaSnt, "*") != 0)
					{

						rawSum = strstr(nmeaSnt, "*");

						memcpy(smNmbr, &rawSum[1], 2);

						smNmbr[2] = '\0';

						intSum = nmea0183_checksum(nmeaSnt);

						// "%X" unsigned hexadecimal integer (capital letters)
						sprintf(hex, "%X", intSum);

						// checksum data verification, if OK, then we can really trust
						// the data in the the NMEA sentence
						int empties[12];
						memset(empties, 0, sizeof(empties));
						if (strstr(smNmbr, hex) != NULL)
						{
							int i=0, j=0, empties_n=0;
							while(nmeaSnt[i]!='\0')
							{
								if(nmeaSnt[i]==',' && nmeaSnt[i+1]==',')
								{
									empties_n++;
									empties[j]=empties_n;
									j++;
								}
								else if(nmeaSnt[i]==',' && nmeaSnt[i+1]!=',')
								{
									empties_n++;
								}
								else if(nmeaSnt[i]==',' && nmeaSnt[i+1]=='*')
								{
									empties_n++;
									empties[j]=empties_n;
									j++;
								}

								i++;
							}
							i=0;
							//printf("STRING:%s\n",nmeaSnt);

							// we want to send the string "nmeaSnt"
							// splitting the good NMEA sentence into the tokens by the comma delimiter
							/*for (char *pV = strtok(nmeaSnt, ","); pV != NULL; pV = strtok(NULL, ",")) {
								printf("STRING:%s\n",pV);
								printf("CNT %d and empties[i] %d\n\r",cnt,empties[i]);
								fflush(stdout);
								while(cnt==empties[i])
								{
									i++;
									cnt++;
								}
								switch (cnt) {

									case 1:
										daytime_raw=strdup(pV);
										printf("1: %s\n\r",daytime_raw);
										break;
									case 2:
										valid_raw=strdup(pV);
										printf("2: %s\n\r",valid_raw);
										if(strcmp(valid_raw,"V"))
										{
											GPS_retry=1;
											pV=NULL;
										}
										else
										{
											GPS_retry=0;
										}
										break;
									case 3:
										lat_raw=strdup(pV);
										printf("3: %s\n\r",lat_raw);
										break;
									case 4:
										hemLat_raw=strdup(pV);
										printf("4: %s\n\r",hemLat_raw);
										break;
									case 5:
										lon_raw=strdup(pV);
										printf("5: %s\n\r",lon_raw);
										break;
									case 6:
										hemLon_raw=strdup(pV);
										printf("6: %s\n\r",hemLon_raw);
										break;
									case 7:
										speed_raw=strdup(pV);
										printf("7: %s\n\r",speed_raw);
										break;
									case 8:
										track_raw=strdup(pV);
										printf("8: %s\n\r",track_raw);
										break;
									case 9:
										date_raw=strdup(pV);
										printf("9: %s\n\r",date_raw);
										break;
									case 10:
										variation_raw=strdup(pV);
										printf("10: %s\n\r",variation_raw);
										break;
									case 11:
										orientation_raw=strdup(pV);
										printf("11: %s\n\r",orientation_raw);
										break;
								}
								fflush(stdout);
								cnt++;
							}  // end for()*/
							//cnt=0;
						} // end of of the checksum data verification


						//send the data to spi here


					} // end of $GNGLL sentences selection
					/*
					if (strstr(nmeaSnt, "$GPVTG") != 0 && strlen(nmeaSnt) > 29 && strstr(nmeaSnt, "*") != 0)
					{

							rawSum = strstr(nmeaSnt, "*");

							memcpy(smNmbr, &rawSum[1], 2);

							smNmbr[2] = '\0';

							intSum = nmea0183_checksum(nmeaSnt);

							// "%X" unsigned hexadecimal integer (capital letters)
							sprintf(hex, "%X", intSum);

							// checksum data verification, if OK, then we can really trust
							// the data in the the NMEA sentence
							int empties[12];
							memset(empties, 0, sizeof(empties));
							if (strstr(smNmbr, hex) != NULL) {
								int i=0, j=0, empties_n=0;

								while(nmeaSnt[i]!='\0')
								{
									if(nmeaSnt[i]==',' && nmeaSnt[i+1]==',')
									{
										empties_n++;
										empties[j]=empties_n;
										j++;
									}
									else if(nmeaSnt[i]==',' && nmeaSnt[i+1]!=',')
									{
										empties_n++;
									}
									else if(nmeaSnt[i]==',' && nmeaSnt[i+1]=='*')
									{
										empties_n++;
										empties[j]=empties_n;
										j++;
									}

										i++;
									}
									i=0;
							}
							//send the data to spi here
							//printf("STRING:%s\n",nmeaSnt);

					}// end of $GNVTG sentences selection*/
				}
			}
#endif
				// END GPS READINGS ///////////////////////////////////////////////////////////////////////

				// SUSPENSION READINGS ////////////////////////////////////////////////////////////////////
#if defined(POT_Enable)
				/*suspension1=value[0];
				suspension2=value[1];*/
#endif
				// END SUSPENSION READINGS ////////////////////////////////////////////////////////////////

				// START ICM READINGS /////////////////////////////////////////////////////////////////////
#if defined(ICM_Enable)

#if defined(DRCPATTISON)
				uint8_t var;
				ICM_ReadOneByte(INT_STATUS_1,&var);
				if (var & 0x01)
				{
					int16_t accelCount[3], ax, ay, az, aRes;
				    readAccelData(accelCount);  // Read the x/y/z adc values

				    // Now we'll calculate the accleration value into actual g's
				    // This depends on scale being set
				    ax = (float)accelCount[0] * aRes; // - myIMU.accelBias[0];
				    ay = (float)accelCount[1] * aRes; // - myIMU.accelBias[1];
				    az = (float)accelCount[2] * aRes; // - myIMU.accelBias[2];

				    int16_t gyroCount[3], gx, gy, gz, gRes;
				    readGyroData(gyroCount);  // Read the x/y/z adc values

				    // Calculate the gyro value into actual degrees per second
				    // This depends on scale being set
				    gx = (float)gyroCount[0] * gRes;
				    gy = (float)gyroCount[1] * gRes;
				    gz = (float)gyroCount[2] * gRes;

				    int16_t magCount[3], mx, my, mz, magBias[3], mRes;
				    readMagData(magCount);  // Read the x/y/z adc values

				    // Calculate the magnetometer values in milliGauss
				    // Include factory calibration per data sheet and user environmental
				    // corrections
				    // Get actual magnetometer value, this depends on scale being set
				    mx = (float)magCount[0] * mRes - magBias[0];
				    my = (float)magCount[1] * mRes - magBias[1];
				    mz = (float)magCount[2] * mRes - magBias[2];
				  }
#elif defined(CORYCLINE)
				ICM_SelectBank(USER_BANK_0);
				HAL_Delay(10);

				// Obtain accelerometer and gyro data
				ICM_ReadAccelGyroData();

				// Obtain magnetometer data
				ICM_ReadMagData(mag_data);

				// Print raw, but joined, axis data values to screen
				printf(	"(Ax: %u | Ay: %u | Az: %u) \n\r (Gx: %u | Gy: %u | Gz: %u)\n\r"
						"(Mx: %i | My: %i | Mz: %i)\n\r",accel_data[0], accel_data[1], accel_data[2],
						gyro_data[0], gyro_data[1], gyro_data[2],mag_data[0], mag_data[1], mag_data[2]);
				fflush(stdout);
#endif
#endif
				// END ICM READINGS ///////////////////////////////////////////////////////////////////////

				// RECORD SDCARD //////////////////////////////////////////////////////////////////////////

				//tempo,temperaturas,tensão,gps
				HAL_GPIO_WritePin(GPIOC, GPIO_PIN_5, RESET); // SDCard
				HAL_GPIO_WritePin(GPIOB, GPIO_PIN_0, SET);

			    if(file==0){
			    	fresult = f_open(&fil, "file1.txt", FA_CREATE_ALWAYS | FA_WRITE);
			    	file=1;
			    }
			    else{
			    	fresult = f_open(&fil, "file1.txt", FA_OPEN_APPEND | FA_WRITE);
			    }

				clear_buffer();

				/* Writing text */
			    sprintf(buffer, "p1c1 %d  p1c2 %d  p1c3 %d  p1c4 %d  p2c1 %d p2c2 %d p2c3 %d p2c4 %d \n\r", tempack[0][0],tempack[0][1],tempack[0][2],tempack[0][3],tempack[1][0],tempack[1][1],tempack[1][2], tempack[1][3]);
				//sprintf(buffer, "%s \n\r", nmeaSnt);
			    fresult = f_write(&fil, buffer, strlen(buffer), &bw);

			    //printf("%s\r\n",buffer);

				if (fresult != FR_OK){
					printf("Error4: Could not write.\r\n");
				}

				/* Close file */
				fresult = f_close(&fil);

			  	if (fresult != FR_OK){
			  		printf("Error4: Could not close file.\r\n");
			  	}

			  	clear_buffer();

				//printf("%s\r\n",buffer);

			  	fresult = f_open(&fil, "file1.txt", FA_READ);

			  	f_read (&fil, buffer, f_size(&fil), &br);

			  	printf("%s\r\n", buffer);

			  	fresult = fclose(&fil);

			  	clear_buffer();

			  	HAL_GPIO_WritePin(GPIOC, GPIO_PIN_5, SET); // SDCard*/
				///////////////////////////////////////////////////////////////////////////////////////////
				time_count = 0;
		}
	}
}
  /* USER CODE END 3 */


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
/* USER CODE BEGIN 4 */

int nmea0183_checksum(char *msg) {

	int checksum = 0;
	int j = 0;

	// the first $ sign and the last two bytes of original CRC + the * sign
	for (j = 1; j < strlen(msg) - 4; j++) {
		checksum = checksum ^ (unsigned) msg[j];
		//printf("byte: %c\n\r",msg[j]);
		fflush(stdout);
	}

	printf("CKSUM %d\n\r", checksum);
	return checksum;

}

void HAL_UART_RxHalfCpltCallback(UART_HandleTypeDef *huart) {

	GPS_ready = 1;

}

void HAL_UART_RxCpltCallback(UART_HandleTypeDef *huart) {

	GPS_ready = 0;

}

int bufsize (char *buf)
{
	int i=0;
	while (*buf++ != '\0') i++;
	return i;
}

void clear_buffer (void)
{
	for (int i=0; i<BUFFER_SIZE; i++) buffer[i] = '\0';
}

/* USER CODE END 4 */
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


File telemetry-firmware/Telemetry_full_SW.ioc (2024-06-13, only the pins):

Mcu.UserName=STM32F446RETx
PB13.Signal=CAN2_TX
PA12.Signal=CAN1_TX
PB9.Signal=S_TIM2_CH2
PA6.Signal=SPI1_MISO
PB1.Signal=ADCx_IN9
PA15.Signal=GPXTI15
PC5.Signal=GPIO_Output
PA3.Signal=USART2_RX
PA0-WKUP.Signal=UART4_TX
PA13.Signal=SYS_JTMS-SWDIO
PA1.Signal=UART4_RX
PA5.Signal=SPI1_SCK
PA2.Signal=USART2_TX
PB3.Signal=SYS_JTDO-SWO
PB5.Signal=GPIO_Output
PA11.Signal=CAN1_RX
PA14.Signal=SYS_JTCK-SWCLK
PB0.Signal=GPIO_Output
PC1.Signal=ADCx_IN11
PB12.Signal=CAN2_RX
PA7.Signal=SPI1_MOSI

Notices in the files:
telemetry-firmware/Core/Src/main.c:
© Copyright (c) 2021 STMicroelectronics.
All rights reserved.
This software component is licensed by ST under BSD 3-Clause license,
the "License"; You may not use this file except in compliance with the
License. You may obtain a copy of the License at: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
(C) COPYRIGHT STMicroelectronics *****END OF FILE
